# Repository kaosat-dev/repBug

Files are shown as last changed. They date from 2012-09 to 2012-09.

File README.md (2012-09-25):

RepBug , a 3d printable , mini hexapod !
========================================

**Some features:**

- open source design & code
- parametric (modelled in openscad)
- relatively cheap (<200 euros, all included, hopefully)
- showcase the advantages of 3d printing over traditional CNC methods 

**Some more details :**

- muscle: HXT900 micro servos ->9 grams each (X18 for the legs, some more for head etc perhaps)
- brain : RaspberryPi or BeagleBone -> 30 g (this might change, as initial experimentation will be done on Arduino)
- skeleton: small 3d printed parts (PLA plastic), sturdy yet light ! -> 10 g per leg
- senses:
		- sight:
			for simplicity, I will start with a ping ultrasonic sensor
			further down the line :  small cheap chinese webcam , without casing ->3g 
		- touch:
			not fully decided yet, but I will be doing experiments with pressure sensors in the feet

What you fill find in this repository:

**Cad**
	All the openscad files necessary to print the hexapod

**Code**
	the python "host" program / mini server (more on this later)
	the arduino/c++ firmware (and various experiments) 
 
License:
========
GPLV3

Overview
========
Go to http://kaosat-dev.github.com/repBug/ for a more "visual" overview of this project

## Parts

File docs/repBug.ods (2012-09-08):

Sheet: Electronics
Component | Amount | Price | Weight | Price Total (euros) | Weight Total (grams)
16 channel servo ctrl | 2 | 13.69 | 9 | 27.38 | 18
Raspberry-pi | 1 | 35 | 30 | 35 | 30
!hxt900 micro servo | 21 | 2.15 | 9 | 45.15 | 189
webcam | 1 | 1 | 3 | 1 | 3
 |  |  |  | 108.53 | 240
Mini Maestro 24-Channel USB Servo Controller | 1 | 45.49 |  | 45.49 | 12.2

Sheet: Structural Components
Component | Amount | Price | Weight | Price Total (euros) | Price Total
Coxa | 6 | 0 | 3 | 0 | 18
Femur
Tibia
 |  |  |  | 0 | 18

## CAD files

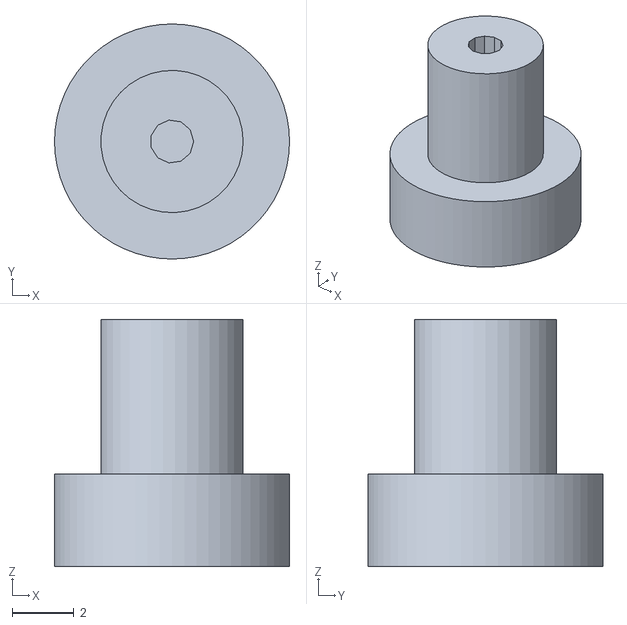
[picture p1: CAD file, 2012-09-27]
cad/stl/coxa_bottom_axis.stl
7.60 x 7.60 x 8.00

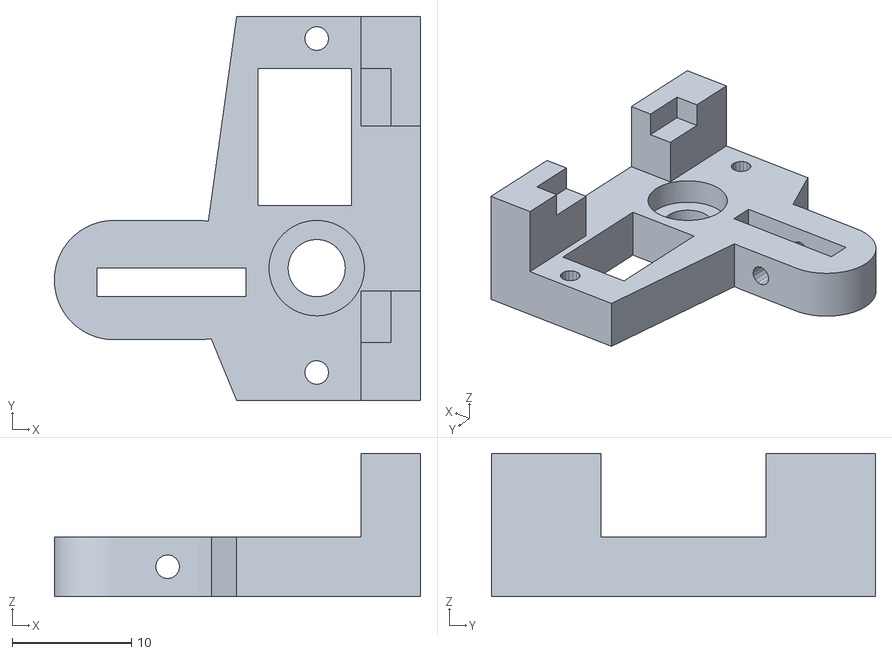
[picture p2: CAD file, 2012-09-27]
cad/stl/coxa_left_bottom.stl
30.7 x 32.2 x 12.0

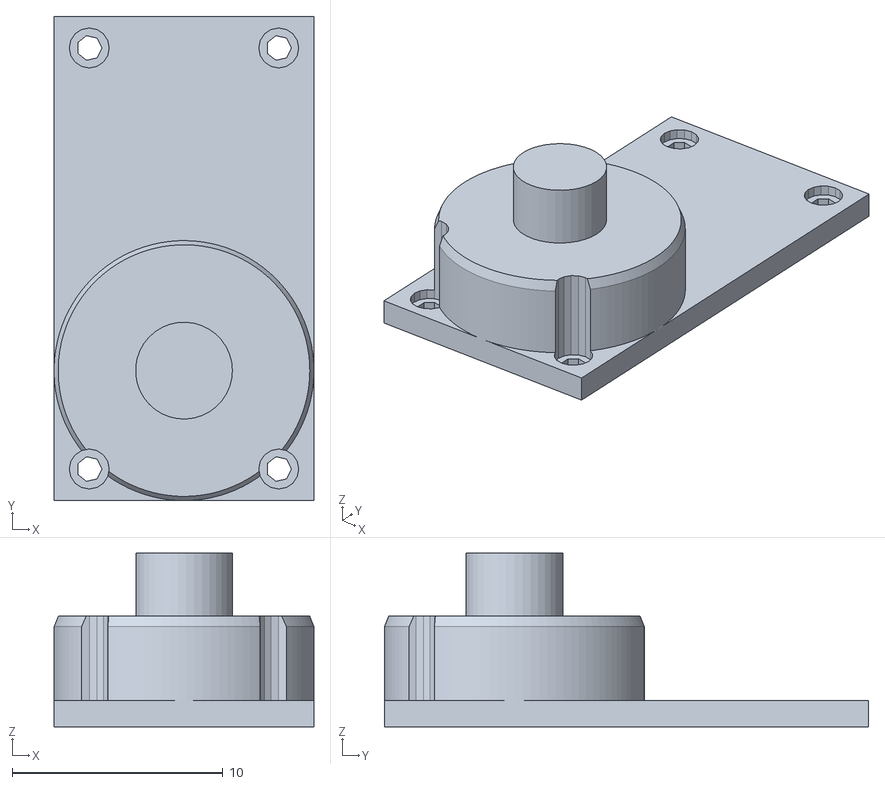
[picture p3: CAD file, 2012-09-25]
cad/stl/servo_back_mod_top.stl
12.3 x 23.0 x 8.26

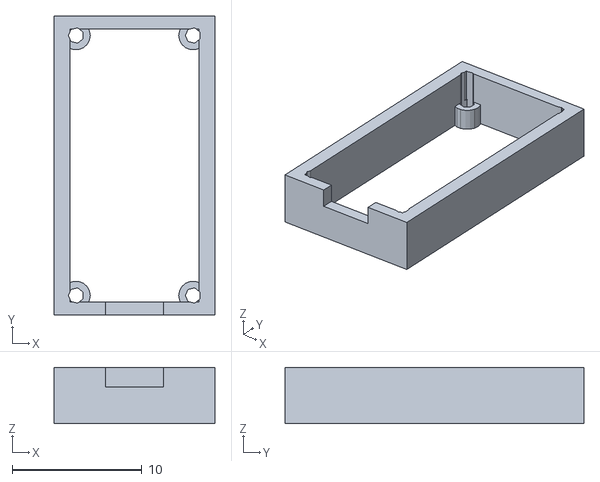
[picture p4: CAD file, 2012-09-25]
cad/stl/servo_back_mod_body.stl
12.3 x 23.0 x 4.34

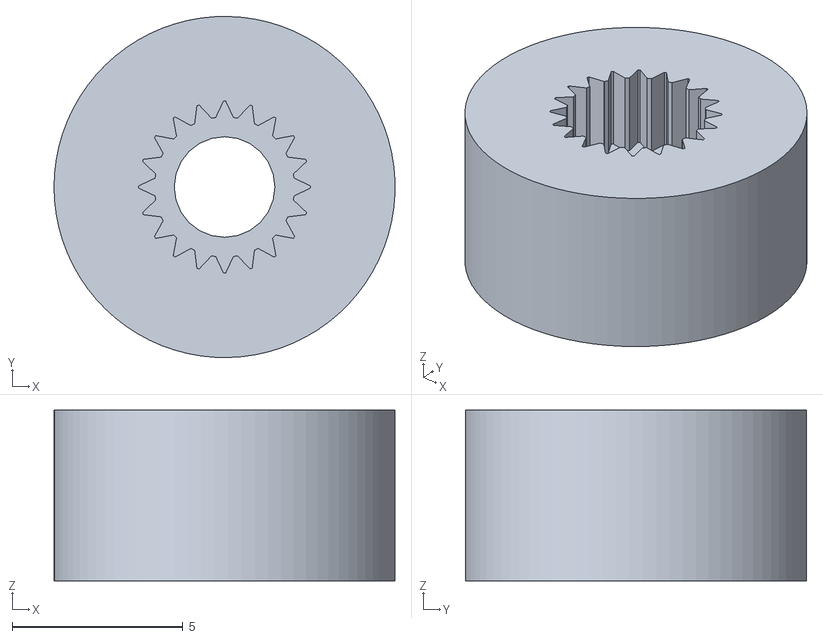
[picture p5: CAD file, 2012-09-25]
cad/stl/servo_mount_hole_test.stl
10.00 x 10.00 x 5.00

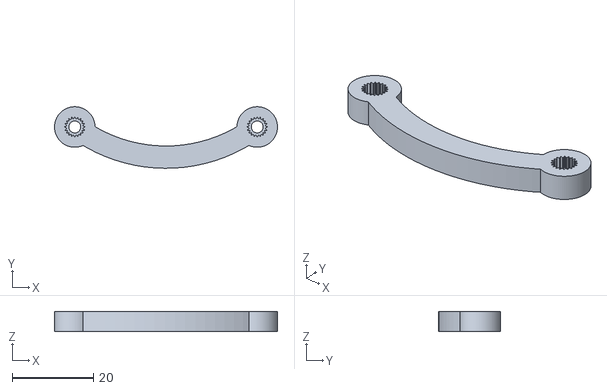
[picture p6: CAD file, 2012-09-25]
cad/stl/femur_2.stl
55.0 x 15.2 x 5.00

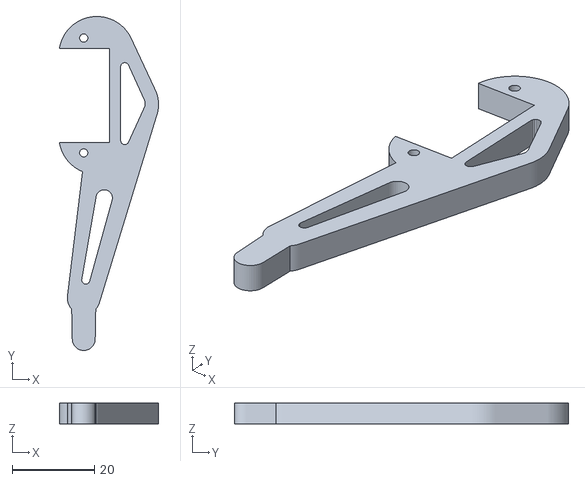
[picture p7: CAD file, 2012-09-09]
cad/stl/tibia2.stl
24.2 x 81.5 x 5.00

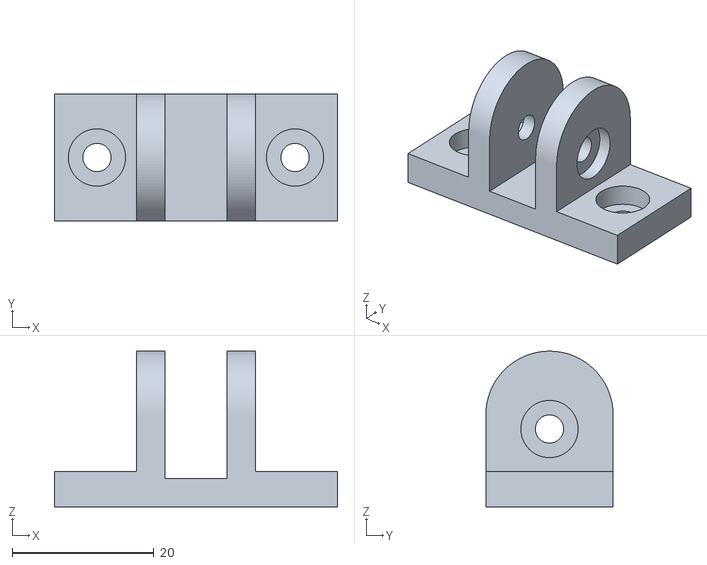
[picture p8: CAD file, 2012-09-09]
cad/stl/prototyper_mast_attach_bottom.stl
40.0 x 18.0 x 22.0

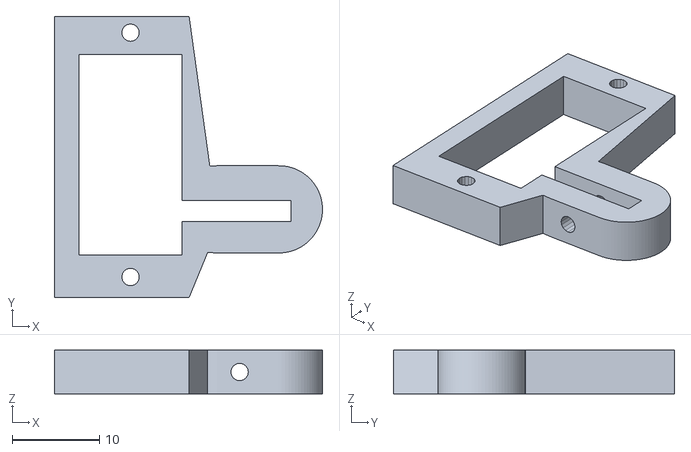
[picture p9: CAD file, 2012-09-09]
cad/stl/coxa_left.stl
30.7 x 32.2 x 5.00

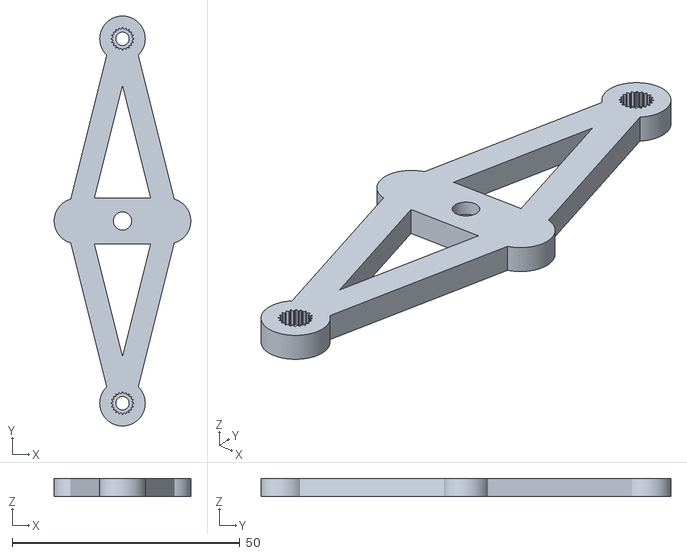
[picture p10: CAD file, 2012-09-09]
cad/stl/prototyper_leg_holder.stl
30.0 x 90.0 x 4.00

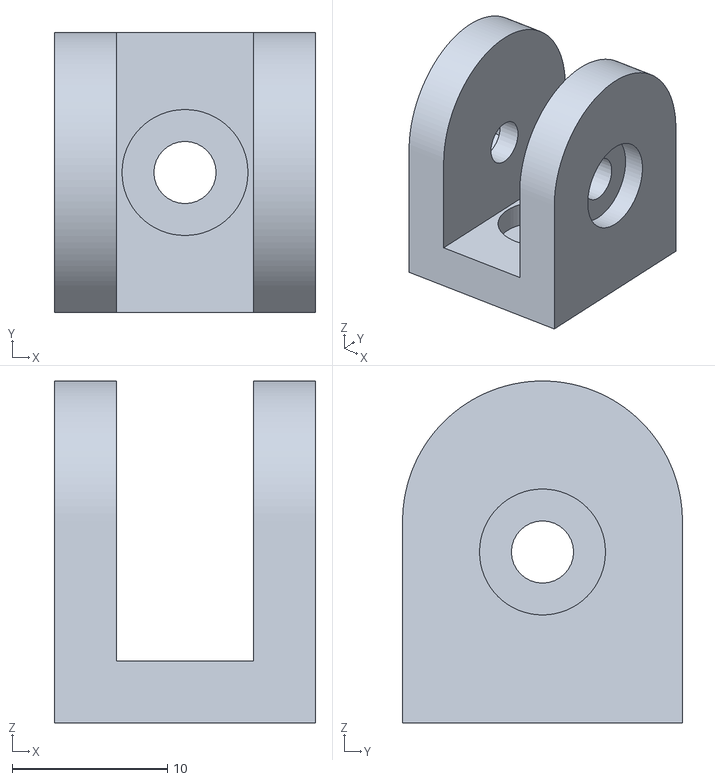
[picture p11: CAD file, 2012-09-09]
cad/stl/prototyper_mast_attach.stl
16.8 x 18.0 x 22.0

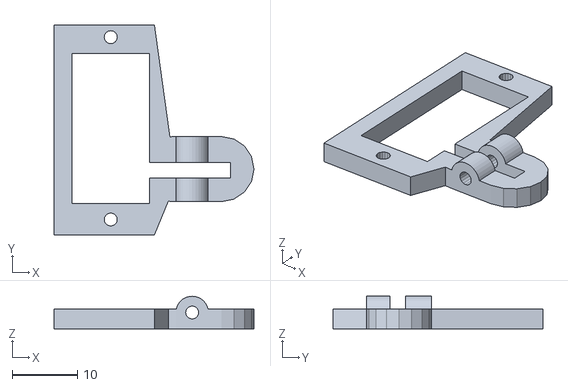
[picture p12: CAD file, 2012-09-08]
cad/stl/coxa.stl
30.7 x 32.2 x 5.00

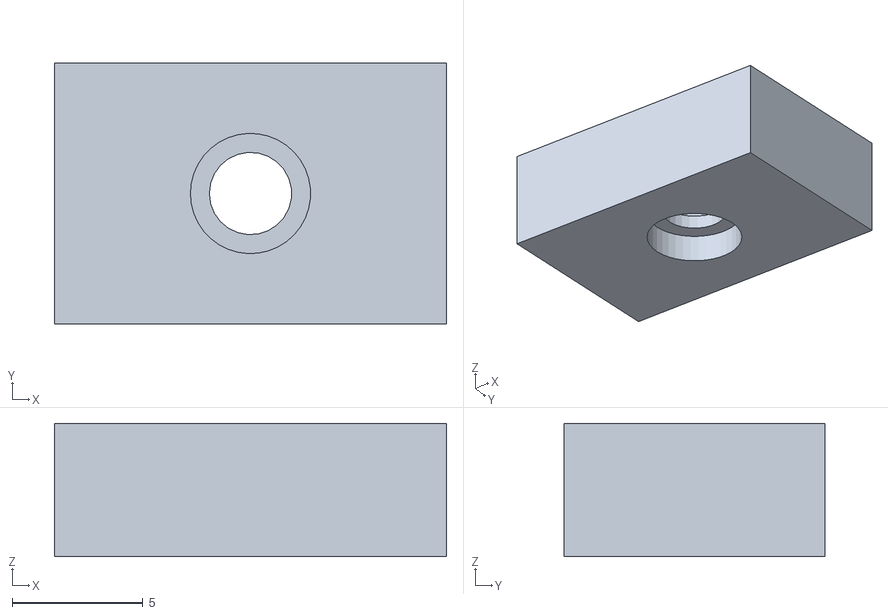
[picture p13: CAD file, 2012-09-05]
cad/stl/servo_test.stl
15.0 x 10.0 x 5.10

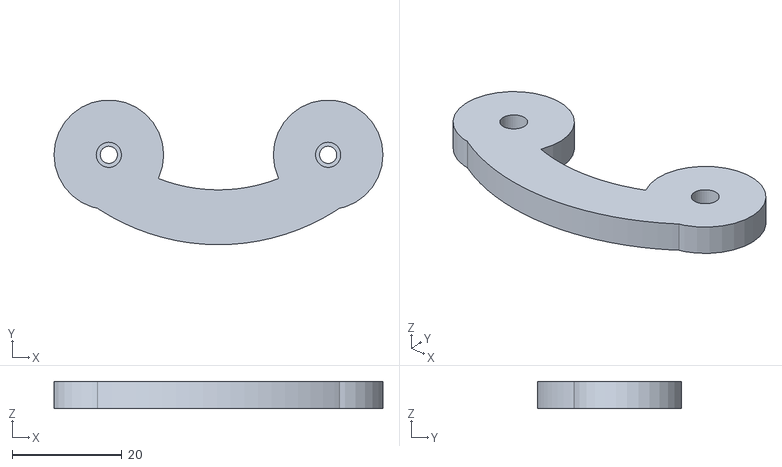
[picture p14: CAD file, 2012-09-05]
cad/stl/femur.stl
60.0 x 26.3 x 5.00

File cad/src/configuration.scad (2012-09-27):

///////////////////////////////
// USER PARAMETERS
///////////////////////////////
xtra=0.1;
tolerance = +0.0001;

servo_width=12.5;
servo_top_width=11.83;
servo_length=23;
servo_height=22.5;

servo_mount_height=16;
servo_mount_length=32;
servo_mount_thickness=2.4;
servo_mount_hole_dia=2;
servo_mount_hole_dist=2.5;
servo_mount_border=4.6;

servo_mount_top_offset=servo_height-(servo_mount_height+servo_mount_thickness);
servo_axis_dia=4.8;

MECHA_COLOR =[ 0.99, 0.85, 0.0 ];// [ 1.0, 0.46, 0.2 ];// [ 0.2, 0.2, 0.2 ]; //
STRUCT_COLOR =[ 0.95, 0.95, 0.95];
SERVO_COLOR = [ 0.25, 0.5, 0.95];//[ 0.5, 0.5, 0.5 ];
ELEC_COLOR =[ 0.5, 0.5, 0.6];

//render settings
VANITY = "vanity";
INDUSTRIAL = "industrial";

//parts definitions

BODY="BODY";
TOP="TOP";
BOTTOM="BOTTOM";
BOTH="BOTH";
NONE="NONE";
AXIS="AXIS";
FULL="FULL";

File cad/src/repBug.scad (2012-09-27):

// repBug
//Licensed under the Creative Commons -Attribution-NonCommercial-ShareAlike licence
// © 2012 by Mark "Ckaos" Moissette

include <utils.scad>
include <configuration.scad>

use <MCAD/involute_gears.scad>
include <MCAD/servos.scad>
include <MCAD/nuts_and_bolts.scad>

///////////////////////////////
// USER PARAMETERS
///////////////////////////////
$fs=0.2; // def 1, 0.2 is high res
$fa=3;//def 12, 3 is very nice

render_mode =VANITY;

///////////////////////////////
// Example usage
////////////////////////////////
repBug();
//repBug_var2();


//eg();
//mirror([1,0,0]) coxa();
//rotate([0,180,0]) femur();
//mirror([1,0,0]) tibia2([0,0,0],[-90,0,0]);
//rotate([0,-90,0])testsdf();

//servo_mount_hole2();
//mount_hole_test();

//leg_movement_protoyper();
//rotate([0,180,0]) servo_back_mod();
//servo_back_mod(part=TOP);

ping_sensor();
///////////////////////////////
// OpenSCAD SCRIPT
////////////////////////////////

module mount_hole_test(thickness=5)
{
	rotate([0,180,0]) 
	difference()
	{
		cylinder(r=5, h= thickness);
		servo_mount_hole3(total_height=thickness);
	}
}

module repBug(leg_angles=40, legs_dist=52, body_width=100)
{
	module leg_test()
	{
		HXT900([0,0,0]);
		HXT900([13,15,0] ,[90,0,0]);
		HXT900([55,15,0] ,[90,0,0]);
	}

	module half()
	{
		translate([body_width/2,0,0])
		{
		translate([-15,-legs_dist+5,0]) rotate([0,0,-leg_angles]) leg();
		leg();
		translate([-15,legs_dist-5,0]) rotate([0,0,leg_angles])  leg();	
		}
	}
	
	half();
	mirror([1,0,0]) half();

	body([0,0,28]);
	body([0,0,-13]);

	//electronics
	//raspi([0,0,-10]);
	//%ada_servo_driver([30,0,13],[0,90,0]);
}

module repBug_var2(leg_angles=40, legs_dist=52, body_width=100)
{
	module leg_test()
	{
		HXT900([0,0,0]);
		HXT900([13,15,0] ,[90,0,0]);
		HXT900([55,15,0] ,[90,0,0]);
	}

	module half()
	{
		translate([body_width/2,0,0])
		{
		translate([-15,-legs_dist+5,0]) rotate([0,0,-leg_angles]) leg();
		leg();
		translate([-15,legs_dist-5,0]) rotate([0,0,leg_angles])  leg();	
		}
	}
	
	half();
	mirror([1,0,0]) half();

	body([0,0,28]);
	body([0,0,-13]);

	//electronics
	//raspi([0,0,-10]);
	//%ada_servo_driver([30,0,13],[0,90,0]);

}

module leg(doubleFemur=true)
{
	fem_length=45;

	coxa([0,0,0],[0,0,0],femur_servo_mod=doubleFemur);

	femur([13,-10,0],[90,0,0],length=fem_length);
	if (doubleFemur)
	{
		femur([13,24,0],[90,0,0],length=fem_length);
	}

	tibia2([13+fem_length,0,-5],[0,0,0],femur_servo_mod=doubleFemur);
}





module coxa(pos=[0,0,0],rot=[0,0,0],thickness=5, part=FULL,femur_servo_mod=false)
{
	border_size=servo_mount_border;
	width =servo_top_width*2 + 2*border_size;
	length=servo_length+ border_size*2;

	height_offset= servo_mount_thickness+servo_mount_height;
 
	pos_offset = servo_width/2;

	servo_hole_offset=servo_length+servo_mount_hole_dist-servo_width/2;


	femur_mount_hole_offset= -pos_offset-border_size;

	bla_test_offset=servo_length-(servo_mount_height+servo_mount_thickness);//18.6;//servo_height+5;


	module _servo_holder(pos=[0,0,0],rot=[0,0,0])
	{
		translate(pos) rotate(rot) 
		{
			color(MECHA_COLOR)
			difference()
			{
				translate([0,0,height_offset]) 
				union()
				{
				linear_extrude(height=thickness)
				{	
					hull()
					{
						translate([-1,5]) square([servo_top_width+border_size-1,length],center=true);
						translate([1,-1]) square([servo_top_width+border_size,length/4],center=true);
					}
					hull()
					{
						translate([1,-1]) square([servo_top_width+border_size,length/4],center=true);
						translate([10,-1]) circle(r=5);
						translate([17,-1]) circle(r=5);
					}
				}
				if( thickness<5)
				{
					translate([servo_width,-0.5*(servo_mount_thickness+9.6),servo_mount_hole_dist])   rotate([0,90,90])cylinder(r=2.5,h=10, $fn=32);
				}
				}
				translate([-servo_top_width/2,-pos_offset,height_offset-xtra/2])  cube([servo_top_width,servo_length,thickness+xtra]);
				translate([servo_top_width/2,-servo_mount_thickness,height_offset-xtra/2])  cube([servo_width,servo_mount_thickness,thickness+xtra+5]);

				//coxa servo mount holes
				translate([0,-pos_offset-servo_mount_hole_dist,height_offset-xtra/2]) cylinder(r=servo_mount_hole_dia/2,h=thickness+xtra, $fn=16);
				translate([0,servo_hole_offset,height_offset-xtra/2]) cylinder(r=servo_mount_hole_dia/2,h=thickness+xtra, $fn=16);

				//femur servo mount hole
				translate([servo_width,femur_mount_hole_offset,height_offset+servo_mount_hole_dist]) rotate([0,90,90])cylinder(r=servo_mount_hole_dia/2,h=length+xtra, $fn=16);		
		}
	}
	}


	module _servo_holder_bottom(pos=[0,0,0],rot=[0,0,0])
	{
		translate(pos) rotate(rot) 
		{
			color(MECHA_COLOR)
			difference()
			{
				translate([0,0,height_offset]) 
				union()
				{
					linear_extrude(height=thickness+7)
					{
						hull()
						{
							translate([-1,5]) square([servo_top_width+border_size-1,length],center=true);
							translate([1,-1]) square([servo_top_width+border_size,length/4],center=true);
						}
					}
					linear_extrude(height=thickness)
					{
						hull()
						{
							translate([1,-1]) square([servo_top_width+border_size,length/4],center=true);
							translate([10,-1]) circle(r=5);
							translate([17,-1]) circle(r=5);
						}
					}
					if( thickness<5)
					{
						translate([servo_width,-0.5*(servo_mount_thickness+9.6),servo_mount_hole_dist])   rotate([0,90,90])cylinder(r=2.5,h=10, $fn=32);
					}
				}


				
				//support structure cut outs
				translate([4,5,height_offset+3.5+thickness]) cube([servo_top_width+border_size-1,length+xtra,7],center=true);
				
				translate([5,5,height_offset+3.5+thickness]) cube([servo_top_width+border_size+20,length-border_size*4,7],center=true);

				translate([-servo_width/2,-servo_width/2,height_offset+thickness+bla_test_offset])  cube([servo_width,servo_length,40]);


				translate([0,0,height_offset-xtra])cylinder(r=servo_axis_dia/2, h=10);
				translate([0,0,height_offset+thickness/2])cylinder(r=4, h=10);
				//translate([0,0,height_offset-xtra])cylinder(r=servo_width/2, h=thickness/2+xtra);


				//main holes
				translate([-servo_top_width/2+3,-pos_offset+servo_length/2,height_offset])  cube([servo_top_width-4,servo_length/2,thickness+xtra]);
				translate([servo_top_width/2,-servo_mount_thickness,height_offset-xtra/2])  cube([servo_width,servo_mount_thickness,thickness+xtra+5]);

				//coxa servo mount holes
				translate([0,-pos_offset-servo_mount_hole_dist,height_offset-xtra/2]) cylinder(r=servo_mount_hole_dia/2,h=thickness+xtra, $fn=16);
				translate([0,servo_hole_offset,height_offset-xtra/2]) cylinder(r=servo_mount_hole_dia/2,h=thickness+xtra, $fn=16);

				//femur servo mount hole
				translate([servo_width,femur_mount_hole_offset,height_offset+servo_mount_hole_dist]) rotate([0,90,90])cylinder(r=servo_mount_hole_dia/2,h=length+xtra, $fn=16);		
		}
	}
	}

	module bottom_axis()
	{
		rotate([0,180,0])
		difference()
		{
			union()
			{
				translate([0,0,0])cylinder(r=servo_axis_dia/2-xtra, h=5);
				translate([0,0,5])cylinder(r=4-xtra*2, h=3);
			}

			translate([0,0,-xtra]) cylinder(r=0.7,  h=5);
		}

	}

	translate(pos) rotate(rot) 
	{
		if (part==TOP)
		{
			_servo_holder(pos,rot);
		}
		else if (part==BOTTOM)
		{
			_servo_holder_bottom([0,0,-servo_length-thickness],rot);
		}
		else if (part == AXIS)
		{
			bottom_axis();
		}
		else
		{
			_servo_holder(pos,rot);
			_servo_holder_bottom([0,0,-servo_length-thickness],rot);
		}

		if (render_mode == VANITY)
		{
			HXT900();
			HXT900([servo_width,16,1.5] ,[90,0,0],back_mod=femur_servo_mod);
		}
		else
		{
			%HXT900();
			%HXT900([servo_width,16,1.5] ,[90,0,0],back_mod=femur_servo_mod);
		}

	}
}

module femur(pos=[0,0,0],rot=[0,0,0],length=45, thickness=5, mount_dia = 10, mount_holes_dia=4, width=5.5)
{
	translate(pos) rotate(rot) 
	color(MECHA_COLOR)
	difference()
	{
		union()
		{
			linear_extrude(height =thickness)
			{
				circle(r=mount_dia/2); 	
				translate([length,0])  circle(r=mount_dia/2); 	
			}

			translate([length/2,length-mount_dia/1.22-7]) rotate([0,0,40])	arc(width, thickness, length-5, 75 );
		}
		servo_mount_hole3(total_height=thickness);
		servo_mount_hole3([length,0], total_height=thickness);
	}
}

module femur2(pos=[0,0,0],rot=[0,0,0],length=40, thickness=5, mount_dia = 10, mount_holes_dia=4, width=5)
{
	translate(pos) rotate(rot) 
	color(MECHA_COLOR)
	difference()
	{
		union()
		{
			linear_extrude(height =thickness)
			{	
				hull()
				{
					circle(r=mount_dia/2); 	
				}
				hull()
				{
					translate([0,0]) circle(r=width/2+1); 	
					translate([length/4,-3]) circle(r=width/2+1); 
				}
				hull()
				{
					translate([length/4,-3]) circle(r=width/2+1); 
					translate([length/2,-4]) circle(r=width/2+1); 
				}

				/*hull()
				{	
					translate([length/2,-5]) circle(r=width/2+1); 
					translate([length,0])  circle(r=mount_dia/2); 
				}*/
				//translate([length,0])  //circle(r=mount_dia/2); 	
			}
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

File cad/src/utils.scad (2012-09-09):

include <MCAD/nuts_and_bolts.scad>
BOTH = "both";
CAP = "cap";
NUT = "nut";
NAN="nan";
tolerance = +0.0001;


module mount_hole(pos=[0,0,0], dia=4, length=30, cap_len=NAN, nut_len=NAN,variant=BOTH)//pos it that of center
{
		capRad = METRIC_NUT_AC_WIDTHS[dia]/2 + tolerance; 
		nutRad=METRIC_NUT_AC_WIDTHS[dia]/2+tolerance; 

		cap_len_default = METRIC_NUT_THICKNESS[dia]+tolerance; 
		nut_len_default =METRIC_NUT_AC_WIDTHS[dia];


		cap_pos = length/2-cap_len;
		cap_pos_default=  length/2-cap_len_default;

		nut_pos = -length/2;

		translate(pos)
		{
			cylinder(r=dia/2, h =length,center=true);

			if (variant == CAP) 
			{
				//hack, because openscad has no variables
				if (cap_len == NAN)
				{
					translate([0,0,cap_pos_default])cylinder(r=capRad,h=cap_len_default);
				}
				else
				{
					translate([0,0,cap_pos])cylinder(r=capRad,h=cap_len);
				}
			}
			else if(variant == NUT) 
			{
				if(nut_len==NAN)
				{
					translate([0,0,nut_pos]) cylinder(r=capRad,h=nut_len_default, $fn=6);
				}
				else
				{
					translate([0,0,nut_pos]) cylinder(r=capRad,h=nut_len, $fn=6);
				}
			}
			else
			{
				if (cap_len == NAN)
				{
					translate([0,0,cap_pos_default])cylinder(r=capRad,h=cap_len_default);
				}
				else
				{
					translate([0,0,cap_pos])cylinder(r=capRad,h=cap_len);
				}
				if(nut_len==NAN)
				{
					translate([0,0,nut_pos]) cylinder(r=capRad,h=nut_len_default, $fn=6);
				}
				else
				{
					translate([0,0,nut_pos]) cylinder(r=capRad,h=nut_len, $fn=6);
				}
			}	
		}
}

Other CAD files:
cad/stl/tibia2_left.stl
cad/stl/coxa_right.stl
cad/stl/tibia.stl

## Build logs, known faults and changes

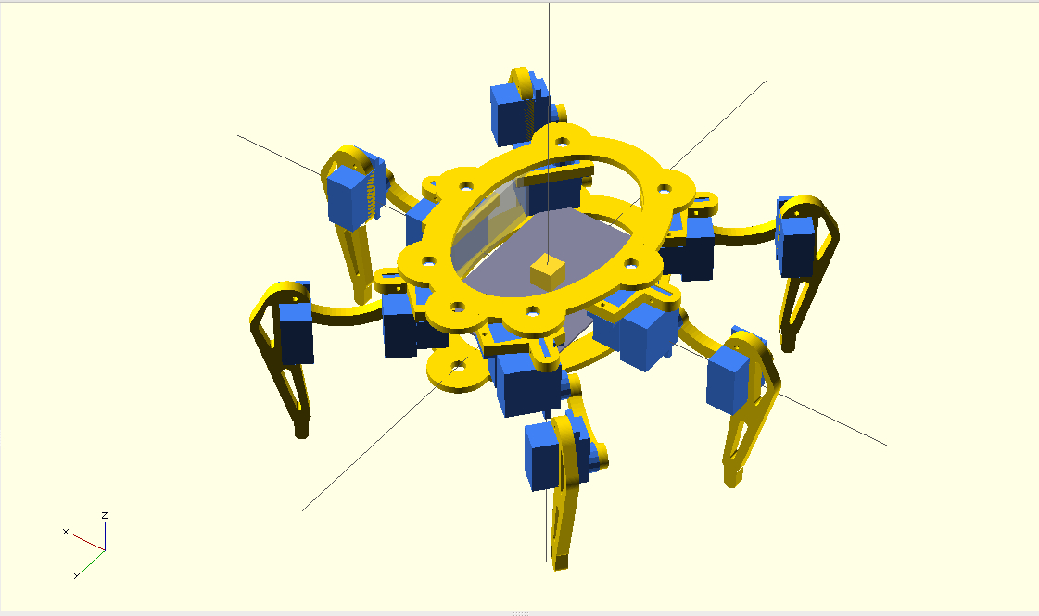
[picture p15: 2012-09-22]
cad/img/repBug_0.1.jpg

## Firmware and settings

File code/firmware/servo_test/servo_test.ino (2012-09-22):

#include <VarSpeedServo.h> 
#include <EEPROM.h>
#include <Wire.h>
#include <Adafruit_PWMServoDriver.h>

#include "Leg.h"
#include "Leg2.h"
#define ledPin 13
#define period 255
char commandBuffer[128];
int commandIndex=0 ;
//72442ba3-058c-4cee-a060-5d7c644f1dbe




volatile int testpos = 200;

void Timer2init() {

    // Setup Timer2 overflow to fire every 8ms (125Hz)
    //   period [sec] = (1 / f_clock [sec]) * prescale * (255-count)
    //                  (1/16000000)  * 1024 * (255-130) = .008 sec
    //0.000000062 * 1024 * (255-130)
    //0.000064 *(255-period)
    TCCR2B = 0x00;        // Disable Timer2 while we set it up

    TCNT2  = period;         // Reset Timer Count  (255-130) = execute ev 125-th T/C clock
    TIFR2  = 0x00;        // Timer2 INT Flag Reg: Clear Timer Overflow Flag
    TIMSK2 = 0x01;        // Timer2 INT Reg: Timer2 Overflow Interrupt Enable
    TCCR2A = 0x00;        // Timer2 Control Reg A: Wave Gen Mode normal
    TCCR2B = 0x07;        // Timer2 Control Reg B: Timer Prescaler set to 1024
}

ISR(TIMER2_OVF_vect) 
{
    ISRUpdateAll();
    TCNT2 = period;     // reset timer ct to 130 out of 255
    TIFR2 = 0x00;    // timer2 int flag reg: clear timer overflow flag
};

Adafruit_PWMServoDriver servoDriver1 = Adafruit_PWMServoDriver();
Leg2 leftLeg= Leg2(servoDriver1, 0,1,2);
Leg2 rightLeg= Leg2(servoDriver1, 3,4,5);

Leg2 leftLeg2= Leg2(servoDriver1, 6,7,8);
Leg2 rightLeg2= Leg2(servoDriver1, 9,10,11);

Leg2 leftLeg3= Leg2(servoDriver1, 12,13,14);
//Leg2 rightLeg3= Leg2(servoDriver1, 9,10,11);
void setup() 
{ 
 // Timer2init();
  servoDriver1.begin();
  servoDriver1.setPWMFreq(50); 
  
  Serial.begin(115200);
  Serial.println("start");   
 // leftLeg.setup();
 // rightLeg.setup();

  /*leftLeg2.coxa.move(0,254);
  leftLeg.femur.move(0,254);
  leftLeg.tibia.move(0,254);
  
  rightLeg.coxa.move(0,254);
  rightLeg.femur.move(0,254);
  rightLeg.tibia.move(0,254);*/
  //attachInterrupt(0, updateAll, CHANGE);
 // TIMSK2 = (0<<OCIE2A) | (1<<TOIE2);
} 
 


char deviceId[37];

//returns this arduino's id
void send_id()
{
   Serial.print(deviceId); 
}
//sets this arduino's id to the specified char array/String
void set_id(char* id)
{
  for (int i=0; i<37; i++) 
  {
    EEPROM.write(i,id[i]);
    deviceId[i]=id[i];
  }
  send_id();
}

//resets this arduino's id to empty (for testing)
void reset_id()
{
   for (int i=0; i<376; i++) 
  {
    EEPROM.write(i,' ');
    deviceId[i]=' ';
  } 
}
//fetches this arduino's id from the eeprom
void get_id()
{ 
  for (int i=0; i<37; i++) 
  {
     deviceId[i] = EEPROM.read(i);
  }
}

int get_pin(char* command,int size)
{
  int pin=0;
  for (int i=1;i<size;i++)
  {

      pin=pin*10+int(command[i])-48;
  }
  return pin;
}


//helper functions

void sub_array(char* data,int start,int end,char* result)
{
  for (int i=start;i<end+1;i++)
  {
      result[i-start]=data[i];
  }
}

int parse_int(char* data,int start,int end)
{
  int result=0;
  boolean neg=false;
 
  if (data[start] == '-')
  {
    neg=true;
    start++;
  }
  for (int i=start;i<end;i++)
  {
      result=result*10+int(data[i])-48;
  }
  
  if(neg == true)
  {
    result=result*-1;
  }
  return result;
}
 
void  parseCommand(char* data, int size)
{

   int markers[64];
   int markerCount=0;
   
   //prepare the marker flags
   for(int i=0;i<size;i++)
   {
     if (data[i]==' ')
     {
       markers[markerCount]=i;
       markerCount+=1;
     }   
   }
   
  int pin;
  markers[markerCount]=size;
  int cmd=parse_int(data,0,markers[0]);
   
    /*Serial.print("command ");
    Serial.print(cmd);
    Serial.print(" total size: ");
    Serial.println(size);*/
    //answer prefix
    Serial.print("ok ");
    Serial.print(cmd);
    Serial.print(" ");
     switch(cmd)
    {
      case 98://debug  test 
        Serial.print("Hello python, Arduino here");
        break;
      case 99://set device id     
      {    
        char tmp[markers[1]-markers[0]+1];
        sub_array(data,markers[0]+1,markers[1],tmp);
        set_id(tmp);
      break;
      }
      case 100://reset device id         
        reset_id();
      break;
      case 2://get device id
        send_id();
      break;
      case 97://setting pin low
        pin=parse_int(data,markers[0]+1,markers[1]);
        digitalWrite(pin, LOW);
        Serial.print(pin);
      break;
      case 96://analog write
      {
        pin=parse_int(data,markers[0]+1,markers[1]);
        int value=parse_int(data,markers[1]+1,markers[2]);
        analogWrite(pin,value);
        Serial.print(pin);
      break;
      }
      case 95://firmware info
       {
        Serial.print("Name: repBug firmware,");
        Serial.print("Version: 0.1");
        break; 
       }
       
      case 9:
      {
        int mov = parse_int(data,markers[0]+1,markers[1]);
        int spd = parse_int(data,markers[1]+1,markers[2]);
        leftLeg.coxa.move(mov, spd);
      /*  Serial.print("Left coxa moving to");
        Serial.print(mov); 
        Serial.print(" At speed (out of 255)");
        Serial.print(spd);
        */
        break; 
      }
      case 10:
      {
        int mov = parse_int(data,markers[0]+1,markers[1]);
        int spd = parse_int(data,markers[1]+1,markers[2]);
        leftLeg.femur.move(mov, spd);
        Serial.print("Left femur moving to");
        Serial.print(mov); 
        Serial.print(" At speed (out of 255)");
        Serial.print(spd);
        break; 
      }
      case 11:
      {
        int mov = parse_int(data,markers[0]+1,markers[1]);
        int spd = parse_int(data,markers[1]+1,markers[2]);
        leftLeg.tibia.move(mov,spd);
        Serial.print("Left tibia moving to");
        Serial.print(mov); 
        Serial.print(" At speed (out of 255)");
        Serial.print(spd);
        break; 
      }
      case 12:
      {
        int mov = parse_int(data,markers[0]+1,markers[1]);
        int spd = parse_int(data,markers[1]+1,markers[2]);
        rightLeg.coxa.move(mov,spd);
        Serial.print("Right coxa moving to");
        Serial.print(mov); 
        Serial.print(" At speed (out of 255)");
        Serial.print(spd);
        
        break; 
      }
      case 13:
      {
        int mov = parse_int(data,markers[0]+1,markers[1]);
        int spd = parse_int(data,markers[1]+1,markers[2]);
        rightLeg.femur.move(mov,spd);
        Serial.print("Right femur moving to");
        Serial.print(mov); 
        Serial.print(" At speed (out of 255)");
        Serial.print(spd);
        break; 
      }
      case 14:
      {
        int mov = parse_int(data,markers[0]+1,markers[1]);
        int spd = parse_int(data,markers[1]+1,markers[2]);
        rightLeg.tibia.move(mov,spd);
        Serial.print("Right tibia moving to");
        Serial.print(mov); 
        Serial.print(" At speed (out of 255)");
        Serial.print(spd);
        break; 
      }
      
      case 15:
      {
        int mov = parse_int(data,markers[0]+1,markers[1]);
        int spd = parse_int(data,markers[1]+1,markers[2]);
        Serial.print("Moving all");
        leftLeg.coxa.move(mov,spd);
        leftLeg.femur.move(mov,spd);
        leftLeg.tibia.move(mov,spd);
        
        rightLeg.coxa.move(mov,spd);
        rightLeg.femur.move(mov,spd);
        rightLeg.tibia.move(mov,spd);
        
       leftLeg2.coxa.move(mov,spd);
        leftLeg2.femur.move(mov,spd);
        leftLeg2.tibia.move(mov,spd);
        
        rightLeg2.coxa.move(mov,spd);
        rightLeg2.femur.move(mov,spd);
        rightLeg2.tibia.move(mov,spd);
        
         leftLeg3.coxa.move(mov,spd);
        leftLeg3.femur.move(mov,spd);
        leftLeg3.tibia.move(mov,spd);
        break; 
      }
      case 16:
      {
        int mov = parse_int(data,markers[0]+1,markers[1]);
        int spd = parse_int(data,markers[1]+1,markers[2]);
        Serial.print("Moving all");
        leftLeg.coxa.move(mov,spd);
        leftLeg.femur.move(mov,spd);
        leftLeg.tibia.move(mov,spd);
        
        rightLeg.coxa.move(mov,spd);
        rightLeg.femur.move(mov,spd);
        rightLeg.tibia.move(mov,spd);
        
       leftLeg2.coxa.move(mov,spd);
        leftLeg2.femur.move(mov,spd);
        leftLeg2.tibia.move(mov,spd);
        
        rightLeg2.coxa.move(mov,spd);
        rightLeg2.femur.move(mov,spd);
        rightLeg2.tibia.move(mov,spd);
        
         leftLeg3.coxa.move(mov,spd);
        leftLeg3.femur.move(mov,spd);
        leftLeg3.tibia.move(mov,spd);
        break; 
      }


      default:
       break;  
    }  
    Serial.println();
}



void loop() 
{ 
  if(Serial.available()>0)
  {
     char c=Serial.read();
    if((c == 10) || (c == 13))
    {
      parseCommand(commandBuffer,commandIndex);
      for (int i=0;i<commandIndex;i++)
      {
        commandBuffer[i]=' ';
      }
      commandIndex=0;
    }
    else
    {
      commandBuffer[commandIndex]=c;
      commandIndex++;
    }
  }
  
  
  updateAll();
  applyAll();
  
} 

void updateAll()
{
  rightLeg.coxa.update();
  rightLeg.femur.update();
  rightLeg.tibia.update();
  
  leftLeg.coxa.update();
  leftLeg.femur.update();
  leftLeg.tibia.update();
  
  rightLeg2.coxa.update();
  rightLeg2.femur.update();
  rightLeg2.tibia.update();

 leftLeg2.coxa.update();
 leftLeg2.femur.update();
 leftLeg2.tibia.update();
 
 leftLeg3.coxa.update();
 leftLeg3.femur.update();
 leftLeg3.tibia.update();

}

void ISRUpdateAll()
{
  rightLeg.coxa.isrUpdate();
  rightLeg.femur.isrUpdate();
  rightLeg.tibia.isrUpdate();
  
  leftLeg.coxa.isrUpdate();
  leftLeg.femur.isrUpdate();
  leftLeg.tibia.isrUpdate();
  
  rightLeg2.coxa.isrUpdate();
  rightLeg2.femur.isrUpdate();
  rightLeg2.tibia.isrUpdate();

 leftLeg2.coxa.isrUpdate();
 leftLeg2.femur.isrUpdate();
 leftLeg2.tibia.isrUpdate();
 
 leftLeg3.coxa.isrUpdate();
 leftLeg3.femur.isrUpdate();
 leftLeg3.tibia.isrUpdate();

}


void applyAll()
{
  rightLeg.coxa.apply();
  rightLeg.femur.apply();
  rightLeg.tibia.apply();
  
  leftLeg.coxa.apply();
  leftLeg.femur.apply();
  leftLeg.tibia.apply();
  
  rightLeg2.coxa.apply();
  rightLeg2.femur.apply();
  rightLeg2.tibia.apply();

 leftLeg2.coxa.apply();
 leftLeg2.femur.apply();
 leftLeg2.tibia.apply();
 
 leftLeg3.coxa.apply();
 leftLeg3.femur.apply();
 leftLeg3.tibia.apply();

}

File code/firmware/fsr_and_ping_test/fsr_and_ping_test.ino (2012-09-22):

#define FSR_PIN 0
#define PING_PIN 22


long duration, cm;

volatile int pingStep=0;//0: emmit low, 1 emmit high, 2 emmit low,3 recieve, 4 result ready
volatile int testVar=0;
volatile long pingDuration=0;

void setup()
{
   pinMode(FSR_PIN, INPUT);
   //initTimer();
   Serial.begin(115200);
   Serial.println("Starting Sensing FORCE and distance");
   
}

void initTimer()
{
  //Interupts
//(target time) = (timer resolution) * (# timer counts + 1)
    cli();          
    TCCR1A = 0;    
    TCCR1B = 0; 
    OCR1A = 65535 ;
    TCCR1B |= (0 << WGM12);
    TCCR1B |= (1 << CS10);
    TCCR1B |= (0 << CS12);
    TIMSK1 |= (1 << OCIE1A);
    
    //TIMSK1 = (1 << TOIE1);
    //TCCR1B |= (1 << CS10);
    sei();
    
    //Timer1 resolution : 16 bits:
    //65535
    //16 Mhz clock :
    //one clock cycle: 1/(16*10^6) = 0.000000062 ie 0.062 us
    //65535 to overflow: ie 65535*0.062 us = 4063.17 us or 0.00406 s
    //how much cycles for 1 us ?:
    //1/0.062 = 16.12 => 16 (more or less)
    
    //(# timer counts + 1) = (target time) / (timer resolution)
    //(# timer counts + 1)= 1us / timer res
    //(# timer counts + 1)= 1us / 0.062 us
    //timercounts+1 = 16000000
    //timercounts = 15999999
    //DUH : max value of OCR1A (or any 16 bit timer is 65535..
    //With an 8 bit timer we can go lower, but loose precision : 255 to overflow ie 255*0.062 us = 15.81 us (min time)
    //250+1=x/0.062us
    //251=x/0.062us
    //251*0.062us=x
    
    //2ms= 32257
}

ISR(TIMER1_COMPA_vect)
{
    //in this case we want to trigger a digitalwrite after 2 Us so around 32 cycles
    testVar++;
     digitalWrite(13, !digitalRead(13));
    if(pingStep==0)
    {
         pinMode(PING_PIN, OUTPUT);
         digitalWrite(PING_PIN, LOW);
         pingStep++;
         testVar=0;
    }
     else if (pingStep==1)
    {
        if(testVar>=2)
        {
            digitalWrite(PING_PIN, HIGH);
            testVar=0;
            pingStep++;
        }
    }
   /*  else if (pingStep==2)
    {
        if(testVar>=5)
        {
            digitalWrite(PING_PIN, LOW);
            testVar=0;
            pingStep++;
        }
    }
      else
  {
    pingStep=0;
    testVar=0;
  }
    else if (pingStep==3)
    {
        pinMode(PING_PIN, INPUT);
        pingDuration = pulseIn(PING_PIN, HIGH);
        pingStep ++;
    }
   
    */
}


void basicPing()
{
   pinMode(PING_PIN, OUTPUT);
   digitalWrite(PING_PIN, LOW);
   delayMicroseconds(2);
   digitalWrite(PING_PIN, HIGH);
   delayMicroseconds(5);
   digitalWrite(PING_PIN, LOW);
   
   pinMode(PING_PIN, INPUT);
   duration = pulseIn(PING_PIN, HIGH);

    cm = microsecondsToCentimeters(duration);
    Serial.print("Distance: ");
    Serial.print(cm);
    Serial.println("cm");
    delay(100);
}
void basicForce()
{
   int force = analogRead(FSR_PIN);
   Serial.print("Force: ");
   Serial.println(force);
}

void isrPing()
{
  if(pingStep==4)
   {
    //TCCR1A = 0;        
    //TCCR1B = 0;
    //TIMSK1 = 0;
     cm = microsecondsToCentimeters(pingDuration);
     Serial.print("Raw duration: ");
     Serial.print(pingDuration);
    Serial.print("Distance: ");
    Serial.print(cm);
    Serial.println("cm");
    delay(100);
    pingStep =0;
    //initTimer();
   }
}


void loop()
{
   basicPing();
   basicForce();
}


long microsecondsToCentimeters(long microseconds)
{
  // The speed of sound is 340 m/s or 29 microseconds per centimeter.
  // The ping travels out and back, so to find the distance of the
  // object we take half of the distance travelled.
  return microseconds / 29 / 2;
}

long ticksToMicroseconds(int ticks)
{
    
}

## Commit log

2012-08-30 Initial commit : basic openscad script + ods for cost and weight calculations
    [repBug.ods, repBug.scad]
2012-09-04 blocking out main shapes and sizes, experimenting, and also modelled the various dimentions of the HXT900 servo horns
    [repBug.scad]
2012-09-05 -basic experimenting and print of servo horn - small changes and print of femur - various experiments with tibia
    [femur.stl, repBug.ods, repBug.scad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]
2012-09-06 -finished first pass for coxa, femur and tibia: all printed and working (but not perfectly of course)
    [coxa.stl, femur_2.stl, repBug.scad]
2012-09-08 - further refinements and tweaks to coxa - attempting to generate splines on the inside of the mount part for femurs etc
    [coxa.stl, femur_2.stl, repBug.ods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]
2012-09-09 - more refinements to tibia , coxa etc - made a set of parts to help with leg movement testing ("prototyping rig") - modified parts (enough for two legs) and rig printed, and ready for testing
    [coxa_left.stl, coxa_right.stl, femur_2.stl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]
2012-09-11 - experimenting with arduino servo control : included arduino code and some awfully basic python for very primitive movement tests
    [repBug.scad]
2012-09-12 - adjusted experimental arduino program: * joint angles now go from -45 to 45 , 0 beeing the default position * added initial rest position ("on belly") - some tweaks to the python test program for b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
2012-09-15 - updated the arduino "firmware" to make use of the LadyAda Pwm/servo driver code * added support for right test leg * added a way to do variable speed with the above (hackish for now) * added a more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
    [Leg.cpp, Leg2.cpp, repBug_test.py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]
2012-09-16 - more experimenting with arduino firmware: * unfortunatly it is NOT possible to use interupts directly with the LadyAda pwm/servo lib, as it uses wire.h which itself uses interupts : "no interupts w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
2012-09-18 - more tweaks and experiments for smoother speed control for the servos - added arduino sketch for first experiments with fsr (force sensor) and ping (ultrasonic range finder) , aswell as interupt (r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
2012-09-22 Restructured project folder structure for more clarity: - seperated cad from code - moved various files around
    [coxa.stl, coxa_left.stl, coxa_right.stl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]
2012-09-22 - added readme - added mindmap to lay down some ideas - some more cleanup
    [coxa.stl, coxa_left.stl, coxa_right.stl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]
2012-09-23 Cad: - added basic version of a replacement bottom for HXT900 servos, to have an "axis" on both side of the servo - added dual femur (making use of the addition above) for more stability - added conf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
    Code:
    - moved arduino files to firmware folder
    [configuration.scad, repBug.scad]
2012-09-25 - Work done on the cad parts: * refined the servo mount hole for tighter fit ... printed two modified femurs and it is an improvement but still fighting the limits of a 0.5 nozzle here * lots of work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
    [configuration.scad, femur_2.stl, repBug.scad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]
2012-09-25 - small cad update: * adjusted various dimentions of the servo back mod, after initial print attempts
    [repBug.scad, servo_back_mod_body.stl, servo_back_mod_top.stl]
2012-09-25 moved scad files to src subfolder
    [configuration.scad, repBug.scad, utils.scad]
2012-09-27 - lots of cad changes * added an experimental lower part for the coxa, that includes "corners" to hold the two servos more tighly, aswell as a possible lower axis for more stability * lots of overall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
    [configuration.scad, coxa_bottom_axis.stl, coxa_left_bottom.stl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]
